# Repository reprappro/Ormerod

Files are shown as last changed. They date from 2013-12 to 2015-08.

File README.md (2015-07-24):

The RepRapPro Ormerod 2 3D Printer design files repository

Licensed under the GPL 3, see: http://www.gnu.org/copyleft/gpl.html

For more information see: https://reprappro.com/shop/reprap-kits/ormerod-2-kit/

Files in this directory were produced in SolidWorks 2015, and is the full assembly for the Ormerod 2. Some components that are shared with our other printers may be found in our "Library" repository.

The 'STLs' directory contains STLs of the printed parts. Instructions for printing parts for Ormerod 2, and a reference - itemising part numbers, descriptions and required quantities - may be found in the Ormerod instructions, here: https://reprappro.com/documentation/ormerod-2/#Printing_parts_for_Ormerod_2

The 'dxf' folder contains the parts in a format for laser cutting.

License GPL

No guarantee is made that the files contained in this project will be free from design faults. The user accepts the risk that some issues may arise from printing and assembling the files contained within this project. Users are however encouraged to publish errors/improvements back to the originator.

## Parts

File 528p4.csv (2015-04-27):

ITEM NO. | PART NUMBER | DESCRIPTION | Category | QTY.
1 | 1009 | 100M PLASTIC REEL OF 1.75 FILAMENT PLA | HARDWARE | 1
2 | 1047 | PCB HEATER (TABBED VERSION) | HARDWARE | 2
3 | 1095 | TCRT1000 | Electronics | 1
4 | 110 | M2.5X5 CAP HEAD | FASTENERS | 2
5 | 111 | M3X8 CAP HEAD | FASTENERS | 5
6 | 112 | M3X25MM CAP SCREW | FASTENERS | 7
7 | 115 | M4X8MM COUNTERSUNK SOCKET SCREW | Fasteners | 1
8 | 116 | M4X12MM COUNTERSUNK SOCKET SCREW | Fasteners | 10
9 | 125 | GLASS PRINTING PLATE | HARDWARE | 1
10 | 185 | MICROSWITCH | HARDWARE | 2
11 | 212 | M3 PLAIN WASHER | FASTENERS | 19
12 | 241 | M3X20MM CAP SCREW | FASTENERS | 2
13 | 257 | M3X12 CAP SCREW | FASTENERS | 16
14 | 258 | M3 NUT | FASTENERS | 46
15 | 279 | 623 BEARING | HARDWARE | 5
16 | 380 | M3X40 CAP HEAD | FASTENERS | 2
17 | 390 | M5X300MM THREADED ROD | Hardware | 1
18 | 394 | DUET | ELECTRONICS | 1
19 | 402 | SMOOTH ROD 12X350MM | Hardware | 4
20 | 407 | Z RUNNER MOUNT | PRINTED PARTS | 1
21 | 408 | NEMA 17 | HARDWARE | 3
22 | 414 | M6X16MM COUNTERSUNK SOCKET SCREW | Fasteners | 7
23 | 423 | MR93ZZ BEARING | Hardware | 1
24 | 424 | M4X16MM BUTTON HEAD CAP SCREW | Fasteners | 3
25 | 425 | Z NUT TRAP V2 | PRINTED PARTS | 1
26 | 429 | M3X8 COUNTERSUNK SCREW | FASTENERS | 2
27 | 437 | Z LOWER MOUNT | PRINTED PARTS | 1
28 | 438 | Z UPPER MOUNT | PRINTED PARTS | 1
29 | 440 | Z GEAR | PRINTED PARTS | 1
30 | 441 | Z GEAR DRIVEN | PRINTED PARTS | 1
31 | 442 | SPOOL SPIGOT | PRINTED PARTS | 1
32 | 443 | LM12LUU | HARDWARE | 1
33 | 444 | LM12UU | Hardware | 5
34 | 452 | 20X40 ALUMINIUM EXTRUSION 350MM | Hardware | 2
35 | 461 | M2.5X10 CAP HEAD | Fasteners | 4
36 | 462 | X IDLER BRACKET | PRINTED PARTS | 1
37 | 465 | M3X50 CAP HEAD | FASTENERS | 6
38 | 466 | M3X12 COUNTERSUNK HEAD | FASTENERS | 7
39 | 467 | M3X20MM COUNTERSUNK SOCKET SCREW | Fasteners | 1
40 | 468 | M3X25MM COUNTERCUNK SOCKET SCREW | Fasteners | 1
41 | 469 | Z MOTOR BRACE | PRINTED PARTS | 1
42 | 473 | X MOTOR BRACKET | PRINTED PARTS | 1
43 | 492 | Z BEARING CLAMP | PRINTED PARTS | 2
44 | 497 | M4 T-NUT | Fasteners | 15
45 | 498 | HEAT SPREADER | HARDWARE | 1
46 | 503 | Z FOOT | PRINTED PARTS | 1
47 | 520 | M3X35 CAP SCREW | FASTENERS | 1
48 | 527 | Z CORNER BRACKET | PRINTED PARTS | 1
49 | 529 | Y AXIS RIB | LASER CUT | 1
50 | 530 | Y AXIS CROSS RIB | LASER CUT | 1
51 | 531 | Y AXIS END PLATE | LASER CUT | 2
52 | 543 | M3X30 CAP SCREW | FASTENERS | 4
53 | 544 | M3X16MM COUNTERSUNK SOCKET SCREW | Fasteners | 4
54 | 545 | PROXIMITY SENSOR PCB | ELECTRONICS | 1
55 | 546 | X Carriage | PRINTED PARTS | 1
56 | 547 | Y IDLER BRACKET | PRINTED PARTS | 1
57 | 548 | Y MOTOR BRACKET | PRINTED PARTS | 1
58 | 549 | Y BEARING BELT CLAMP | PRINTED PARTS | 1
59 | 550 | Y BEARING CLAMP TAGGED | PRINTED PARTS | 1
60 | 561 | X AXIS PLATE | LASER CUT | 1
61 | 562 | X RIB | LASER CUT | 1
62 | 575 | BED CABLE SHIELD | Sheet | 1
63 | 576 | DUET ENCLOSURE BASE | HARDWARE | 1
64 | 577 | DUET ENCLOSURE LID | HARDWARE | 1
65 | 578 | DUET PERIMETER | HARDWARE | 1
66 | 579 | MOTOR SHIELD | SHEET METAL | 1
67 | 581 | VBFS-M3-5-16 | FASTENERS | 4
68 | 582 | MOTOR SHIELD | HARDWARE | 2
69 | 597 | REGULATOR PCB | ELECTRONICS | 1
70 | 641 | SPACER | LASER CUT | 1
71 | 642 | SPOOL MOUNT | LASER CUT | 1
72 | 651 | M4X10mm BUTTON HEAD SCREW | HARDWARE | 6
73 | 681 | BED | LASER CUT | 1
74 | 712 | M5 FULL NUT | FASTENERS | 3
75 | 818 | M3X18MM MALE/FEMALE STANDOFF VBMP-M3-5.0-18 | FASTENERS | 3
76 | 820 | PSU COVER | PRINTED PARTS | 1
77 | 821 | PSU BRACE | PRINTED PARTS | 1
78 | 822 | OUTER PSU PLATE | HARDWARE | 1
79 | 823 | PSU SPACER | HARDWARE | 1
80 | 824 | PSU COVER SPACER | HARDWARE | 1
81 | 825 | INNER PSU PLATE | LASERCUT | 1
82 | 826 | INNER PSU SPACER | LASERCUT | 1
83 | 829 | M4X50MM BUTTON HEAD SOCKET SCREW | Fasteners | 1
84 | 831 | SP-200 12V POWER SUPPLY | HARDWARE | 1

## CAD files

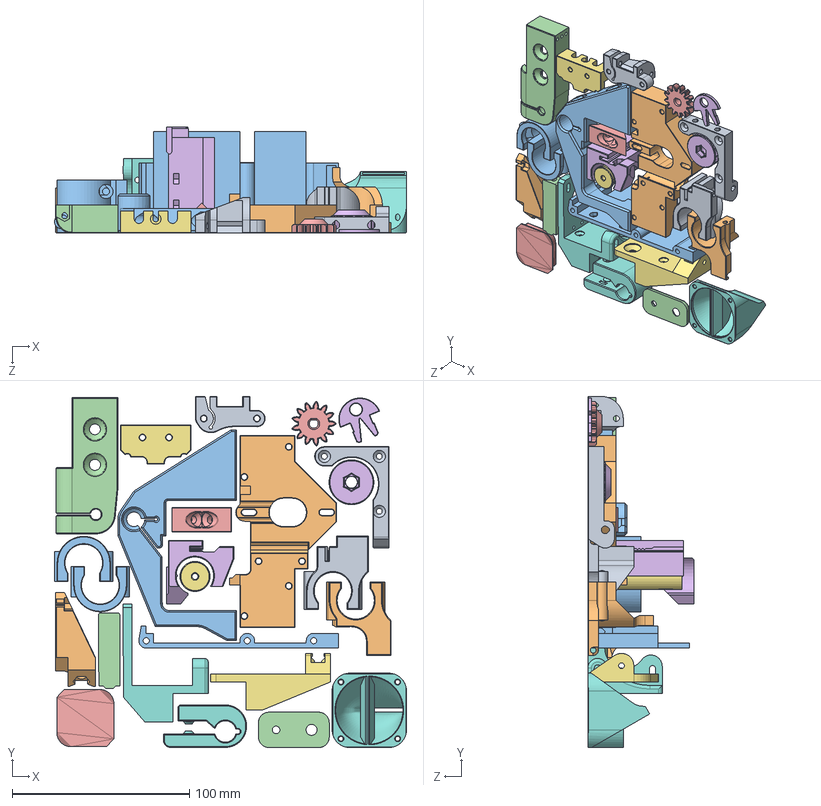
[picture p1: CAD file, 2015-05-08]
PrintTray.SLDASM
198.7 x 198.2 x 60.0 mm
logo

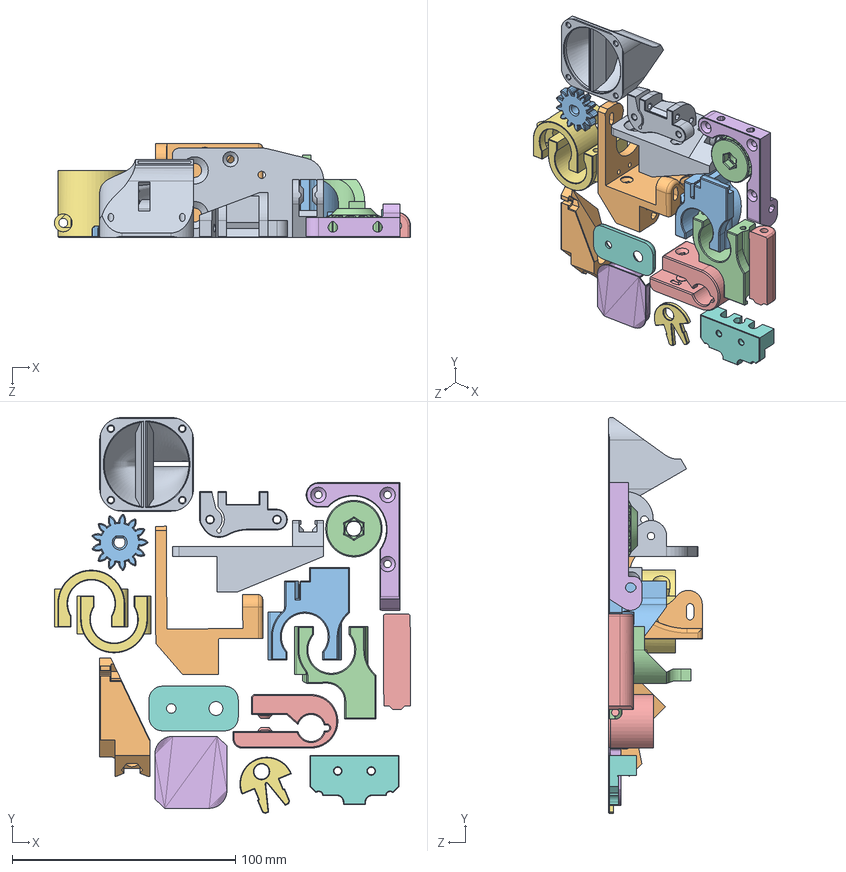
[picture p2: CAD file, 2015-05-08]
DayPrintTrays.SLDASM
159.6 x 177.4 x 42.0 mm
logo

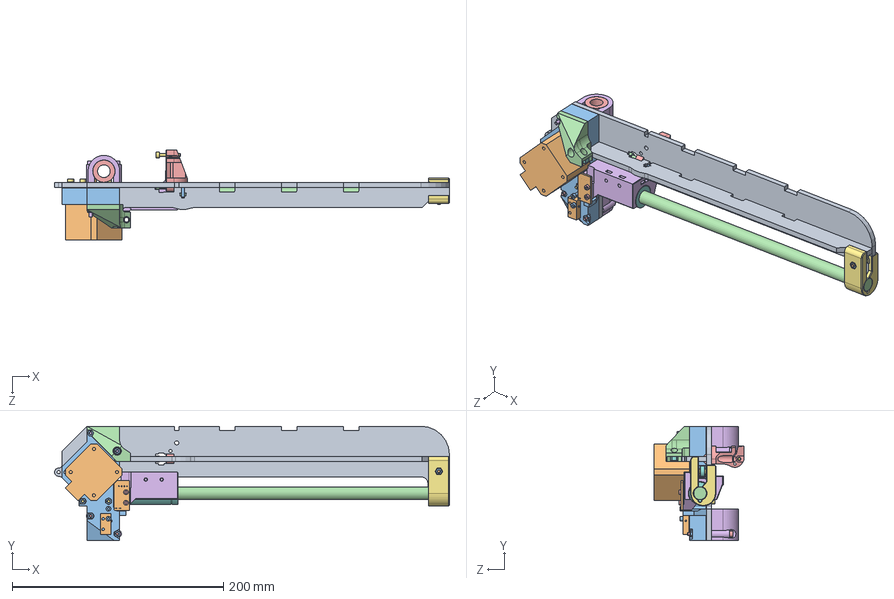
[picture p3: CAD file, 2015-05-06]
760.SLDASM
374.3 x 108.5 x 85.4 mm

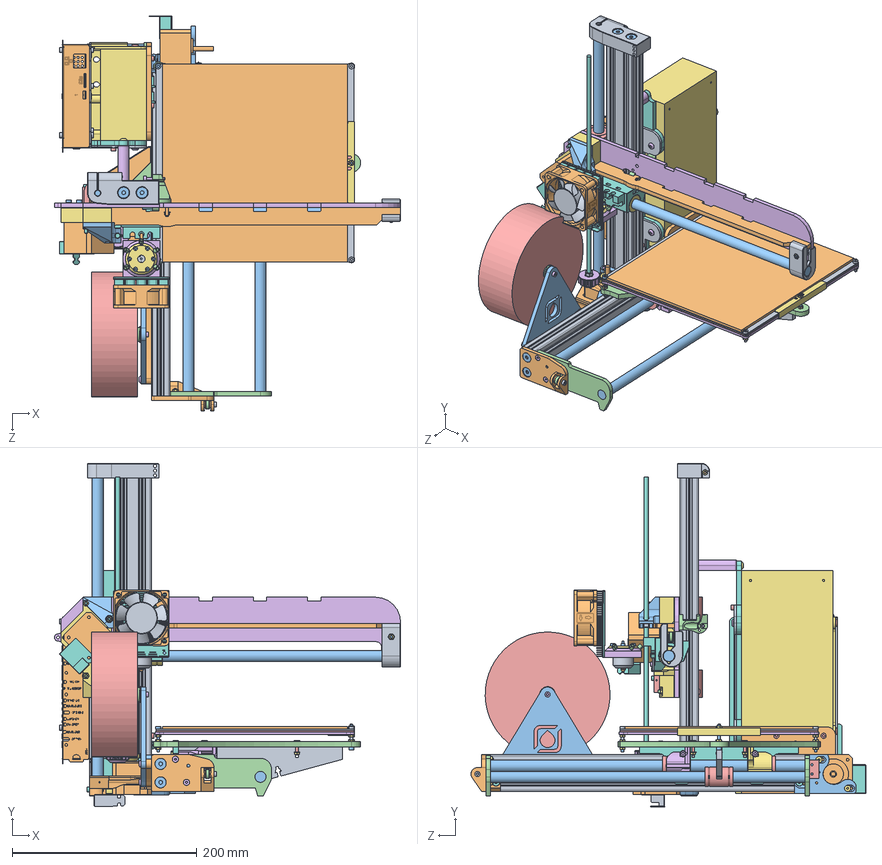
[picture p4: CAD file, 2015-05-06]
528.SLDASM
374.3 x 371.3 x 427.1 mm
Mixing Chamber
Nozzle
Mixer
ThermalBreak x 5
O-Ring
Heatsink Block Bottom
Heatsink Block Top2
m2.5cap screw x 6
60mm Heatsink

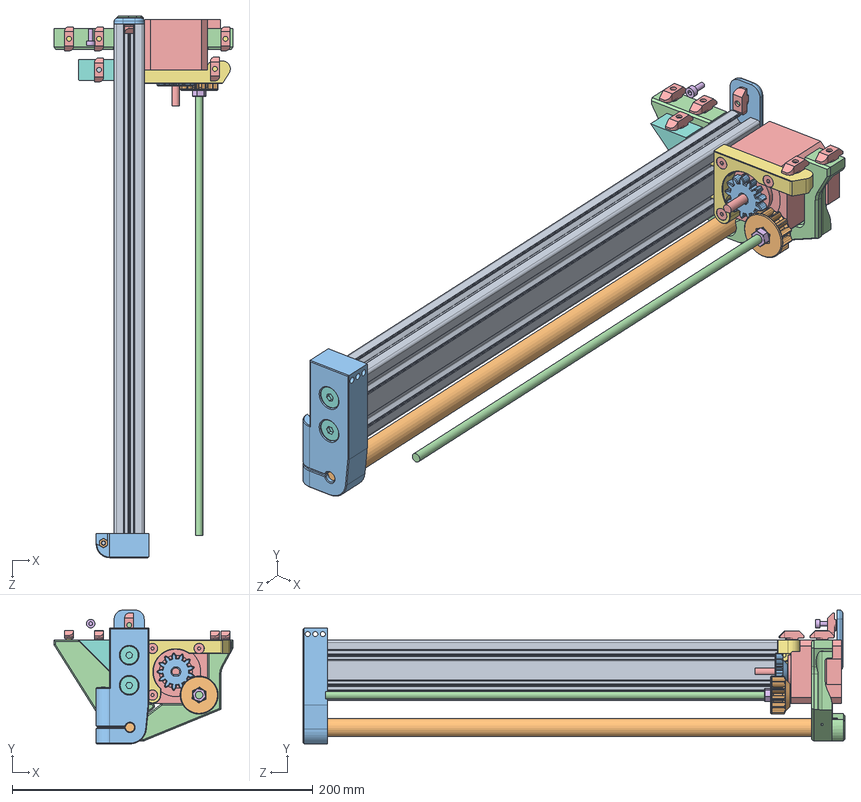
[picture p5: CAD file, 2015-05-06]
750Z.SLDASM
119.0 x 89.0 x 360.0 mm

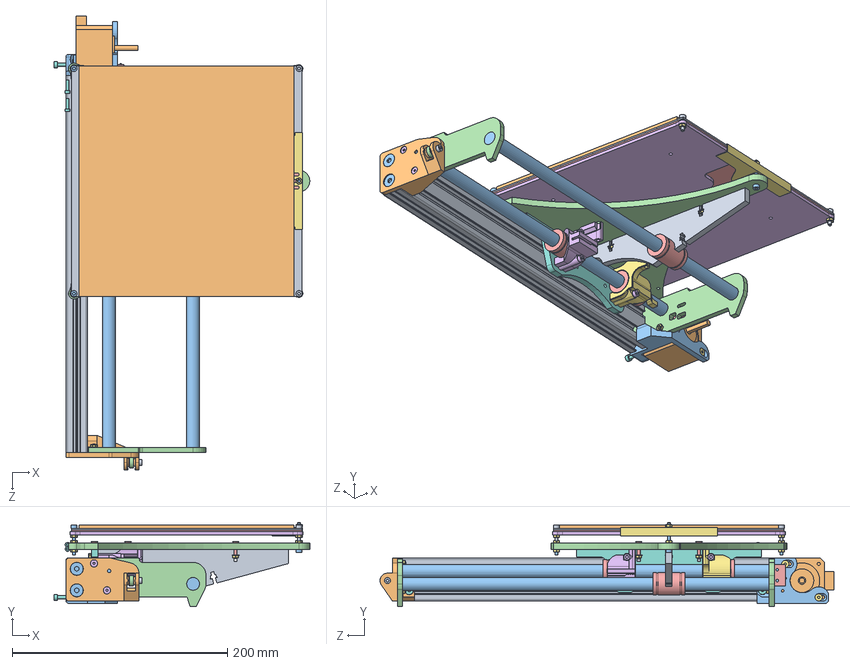
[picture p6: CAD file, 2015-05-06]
750Y.SLDASM
237.4 x 78.0 x 421.5 mm

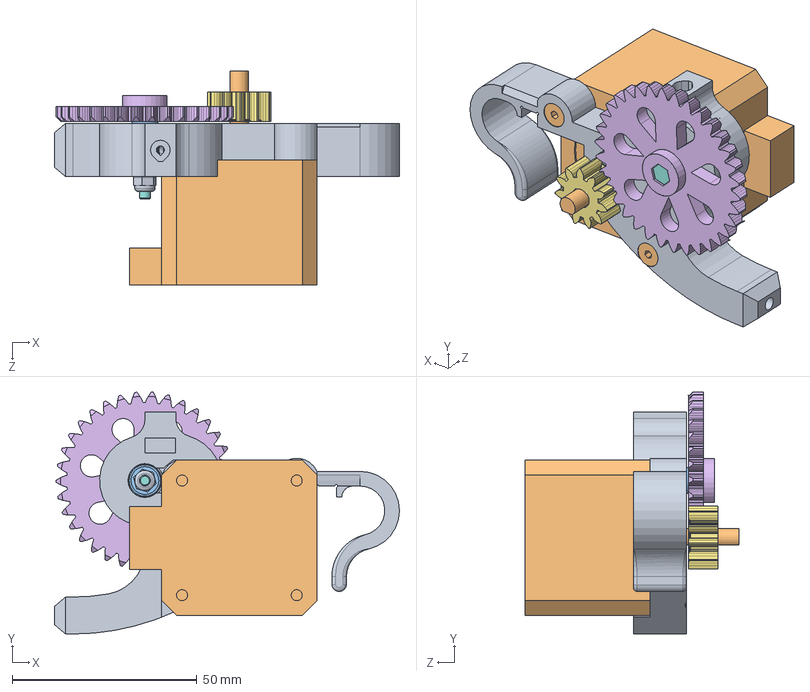
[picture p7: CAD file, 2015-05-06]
733.SLDASM
93.3 x 65.4 x 57.8 mm

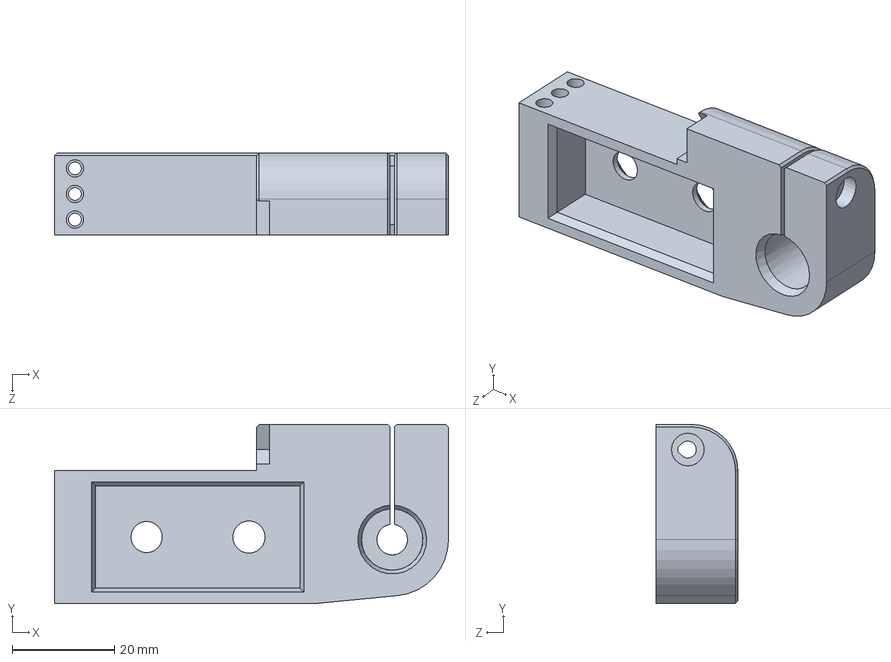
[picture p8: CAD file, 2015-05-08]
438.SLDPRT
77.0 x 35.0 x 16.0 mm

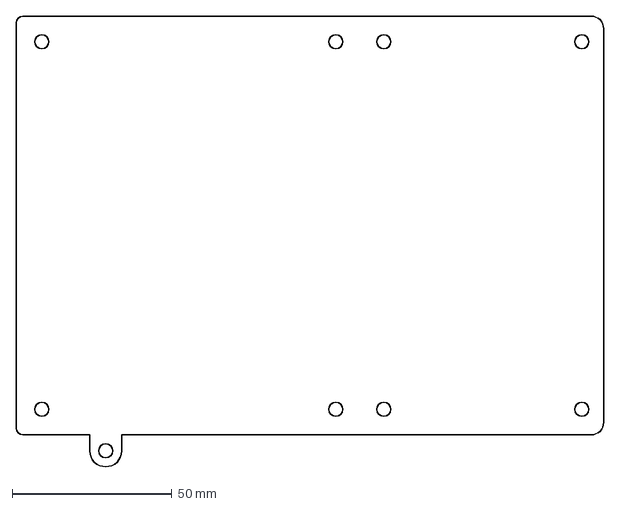
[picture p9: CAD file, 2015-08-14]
dxf/Duet-enclosure-base-expansion.DXF
183.8 x 141.0 mm

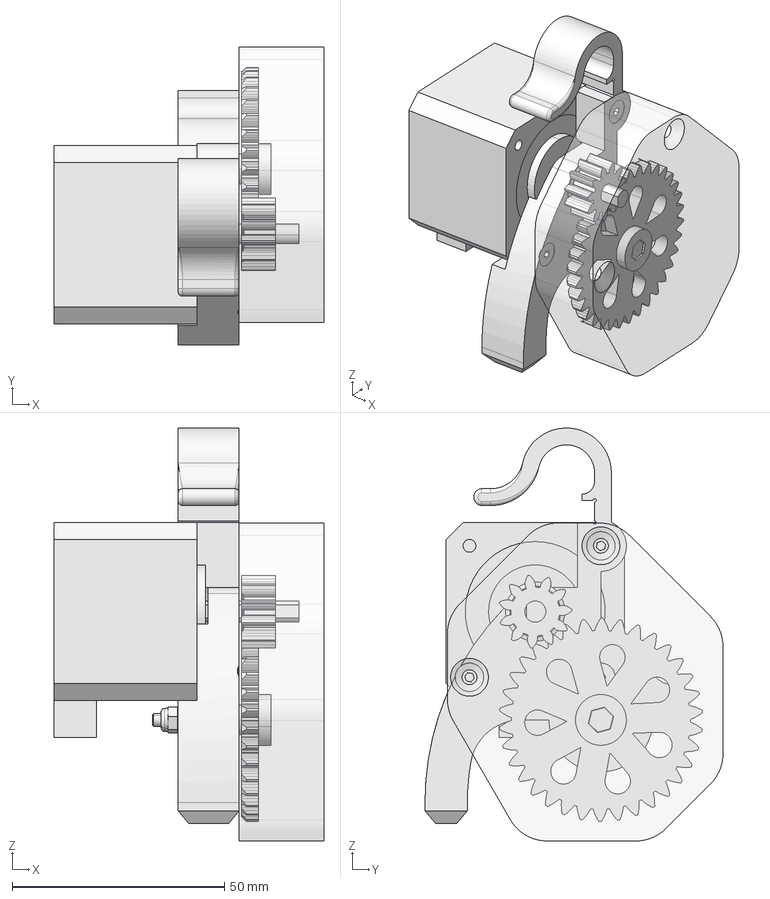
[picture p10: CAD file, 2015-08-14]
freeCAD/extruder-drive-cover.fcstd
63.6 x 70.3 x 97.4 mm
washer
nyloc-nut
big-gear
screw-1
motor
hobbed-drive
bearing-1
screw-3
small-gear
M3-hex-head-screw
screw-2
bearing-2
bearing-3
gear-cover

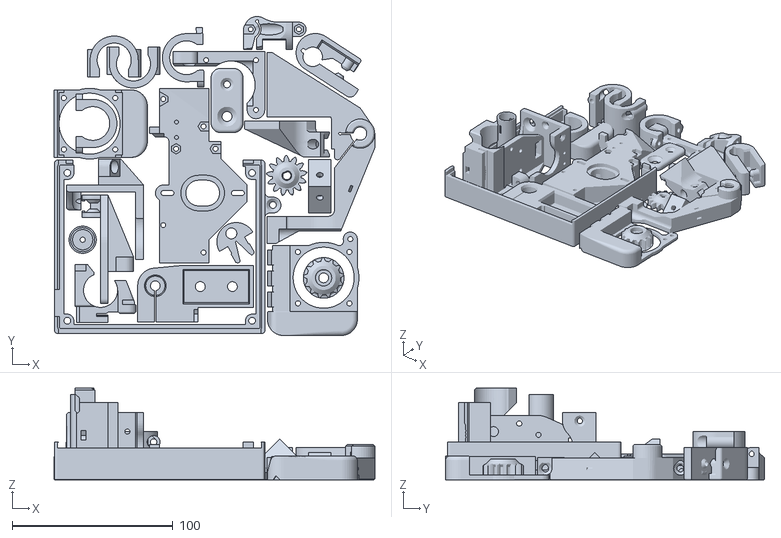
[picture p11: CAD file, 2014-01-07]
stl/build-plate.STL
199.6 x 198.6 x 57.0

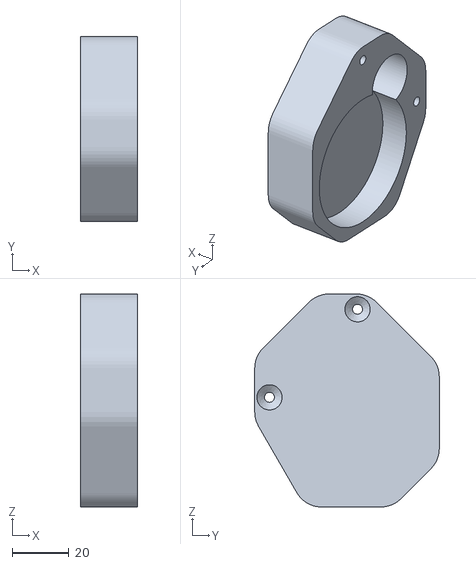
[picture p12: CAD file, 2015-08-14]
stl/individual parts/extruder-gear-cover.stl
20.0 x 65.0 x 75.0

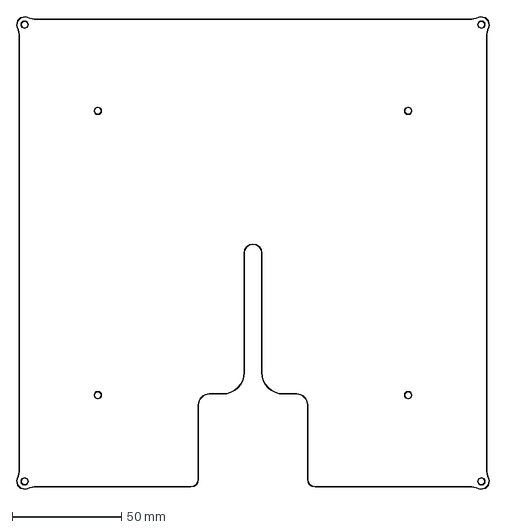
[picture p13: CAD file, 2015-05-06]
dxf/1044.1.DXF
216.6 x 216.6 mm

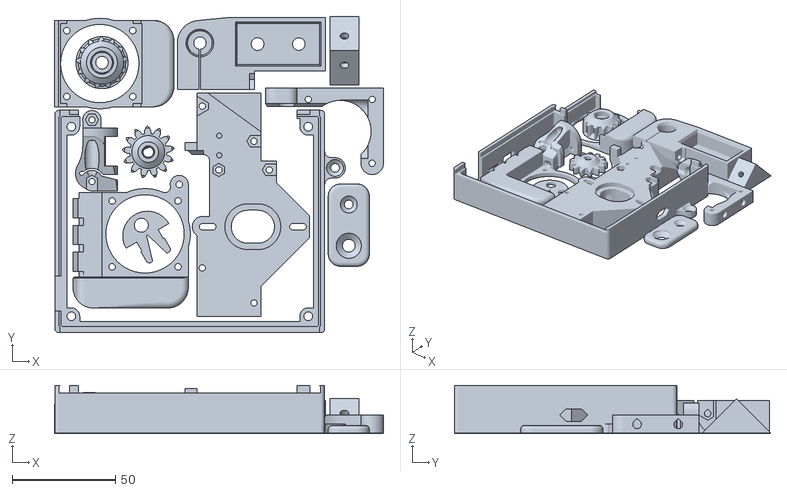
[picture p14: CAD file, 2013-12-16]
stl/build-plate_a.STL
159.7 x 153.6 x 23.5

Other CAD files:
STLs/Trays/528.5AM2.STL
STLs/Trays/528.5PMTray.STL
dxf/561.1.DXF
STLs/Trays/528.5AM1.STL
1044.SLDPRT
1079.SLDPRT
1123.SLDPRT
402.SLDDRW
402.SLDPRT
407.SLDPRT
425.SLDPRT
437.SLDPRT
440.SLDPRT
441.SLDPRT
442.SLDPRT
446.SLDPRT
447.SLDPRT
458.SLDDRW
458.SLDPRT
462.SLDPRT
469.SLDPRT
473.SLDPRT
492.SLDPRT
501.SLDPRT
503.SLDPRT
525.SLDPRT
527.SLDPRT
529.SLDPRT
530.SLDPRT
531.SLDPRT
546.SLDPRT
547.SLDPRT
548.SLDPRT
549.SLDPRT
550.SLDPRT
554.SLDPRT
561.SLDPRT
562.SLDPRT
575.SLDPRT
641.SLDPRT
642.SLDPRT
681.SLDPRT
781.SLDPRT
821.SLDPRT
STLs/1079.STL
STLs/1123.STL
STLs/407.STL
STLs/425.STL
STLs/437.STL
STLs/438.STL
STLs/440.STL
STLs/441.STL
STLs/442.STL
STLs/446.STL
STLs/447.STL
STLs/462.STL
STLs/469.STL
STLs/473.STL
STLs/492.STL
STLs/503.STL
STLs/525.STL
STLs/527.STL
STLs/546.STL
STLs/547.STL
STLs/548.STL
STLs/549.STL
STLs/550.STL
STLs/554.STL
STLs/821.STL
dxf/1044.DXF
dxf/531.1.DXF
dxf/575.0.DXF
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

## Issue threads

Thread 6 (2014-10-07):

build-plate_a.stl casues error in Slic3r 1.1.7

OricTosh, 2014-10-07:
The build plate_a  STL file for the Ormerod causes an error in Slic3r 1.1.7 it won't slice the file.
I put the file into netfabb basic and repaired the file. I'm now able to slice the file with no errors.

RRP-support, 2015-10-05:
This is an automated reply to your message "Re: [Ormerod] build-plate_a.stl casues error in Slic3r 1.1.7 (#6)" sent to support@reprappro.com.

Dear Chris Hills <notifications@github.com>

Thank you for your email. We endeavour to answer all emails within 24 hours. It may take longer during busy times, and holiday periods. We process all customer queries on a first come first served basis, during our office hours which are 9am to 5pm GMT Mon-Fri.

Other support channels are available. Please refer to the relevant troubleshooting guide for your machine:

Ormerod 2: https://reprappro.com/documentation/ormerod-2/troubleshooting/
Ormerod: https://reprappro.com/documentation/ormerod/troubleshooting/

Huxley Duo: https://reprappro.com/documentation/huxley-duo/troubleshooting/
Huxley: https://reprappro.com/documentation/huxley/troubleshooting/

Mono and Tricolour Mendel: https://reprappro.com/documentation/mendel-tricolour/troubleshooting/

Support is also available from other owners of RepRapPro and other 3D printers, either through the RepRap Forums: https://forums.reprap.org or through IRC which can be accessed from here: https://reprappro.com/support-channel/ (works on Chrome, not Firefox).

Best regards,

RepRapPro Support Team.

RRP-support, 2015-10-05:
Is that one of the build plates for the Ormerod 1 384 or Ormerod 2 528.4? It's probably better use the latest parts, unless you need the Ormerod 1 y-axis parts, in which case just print them.
Ian
RepRapPro tech support.

OricTosh, 2015-10-05:
Hi Ian,

Yes it was a build plate for an ormerod 2 528.4;
I closed the issue as it was sometime ago and has probably been fixed
with a newer set of STL files as you suggested, so no need to keep it open.

Regards
Chris Hills

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

RRP-support, 2015-10-05:
Ah! Yes, now I see. Thanks!
Ian
RepRapPro tech support

Closed 2015-10-05.

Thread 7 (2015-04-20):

Impossible to know what anything is.....

shadow651, 2015-04-20:
The way this library is now set up (all files are numbered, I assume using some internal part number system), there is no way to know what any file is without opening them. This makes searching for anything specific particularly difficult.

It would be great if a key listing each part and it's corresponding number could be added.

RRP-support, 2015-04-20:
This is an automated reply to your message "[Ormerod] Impossible to know what anything is..... (#7)" sent to support@reprappro.com.

Dear Joseph Dufour <notifications@github.com>

Thank you for your email. We endeavour to answer all emails within 24 hours. It may take longer during busy times, and holiday periods. We process all customer queries on a first come first served basis, during our office hours which are 9am to 5pm GMT Mon-Fri.

Other support channels are available. Please refer to the relevant troubleshooting guide for your machine:

Ormerod 2: https://reprappro.com/documentation/ormerod-2/troubleshooting/
Ormerod: https://reprappro.com/documentation/ormerod/troubleshooting/

Huxley Duo: https://reprappro.com/documentation/huxley-duo/troubleshooting/
Huxley: https://reprappro.com/documentation/huxley/troubleshooting/

Mono and Tricolour Mendel: https://reprappro.com/documentation/mendel-tricolour/troubleshooting/

Support is also available from other owners of RepRapPro and other 3D printers, either through the RepRap Forums: https://forums.reprap.org or through IRC which can be accessed from here: https://reprappro.com/support-channel/ (works on Chrome, not Firefox).

Best regards,

RepRapPro Support Team.

reprappro, 2015-04-20:
And there is. The README mentions the BOM.xlsx file which lists all the part numbers and descriptions.

RRP-support, 2015-04-20:
This is an automated reply to your message "Re: [Ormerod] Impossible to know what anything is..... (#7)" sent to support@reprappro.com.

Dear reprappro <notifications@github.com>

Thank you for your email. We endeavour to answer all emails within 24 hours. It may take longer during busy times, and holiday periods. We process all customer queries on a first come first served basis, during our office hours which are 9am to 5pm GMT Mon-Fri.

Other support channels are available. Please refer to the relevant troubleshooting guide for your machine:

Ormerod 2: https://reprappro.com/documentation/ormerod-2/troubleshooting/
Ormerod: https://reprappro.com/documentation/ormerod/troubleshooting/

Huxley Duo: https://reprappro.com/documentation/huxley-duo/troubleshooting/
Huxley: https://reprappro.com/documentation/huxley/troubleshooting/

Mono and Tricolour Mendel: https://reprappro.com/documentation/mendel-tricolour/troubleshooting/

Support is also available from other owners of RepRapPro and other 3D printers, either through the RepRap Forums: https://forums.reprap.org or through IRC which can be accessed from here: https://reprappro.com/support-channel/ (works on Chrome, not Firefox).

Best regards,

RepRapPro Support Team.

shadow651, 2015-04-20:
This list appears to be incomplete, I can't find the nozzle mount on it (maybe this is a separate issue)

I assume that the Nozzle mount is shared by multiple printers, and thus would be in the Library repository, but that one doesn't appear to have a key.

RRP-support, 2015-04-20:
This is an automated reply to your message "Re: [Ormerod] Impossible to know what anything is..... (#7)" sent to support@reprappro.com.

Dear Joseph Dufour <notifications@github.com>

Thank you for your email. We endeavour to answer all emails within 24 hours. It may take longer during busy times, and holiday periods. We process all customer queries on a first come first served basis, during our office hours which are 9am to 5pm GMT Mon-Fri.

Other support channels are available. Please refer to the relevant troubleshooting guide for your machine:

Ormerod 2: https://reprappro.com/documentation/ormerod-2/troubleshooting/
Ormerod: https://reprappro.com/documentation/ormerod/troubleshooting/

Huxley Duo: https://reprappro.com/documentation/huxley-duo/troubleshooting/
Huxley: https://reprappro.com/documentation/huxley/troubleshooting/

Mono and Tricolour Mendel: https://reprappro.com/documentation/mendel-tricolour/troubleshooting/

Support is also available from other owners of RepRapPro and other 3D printers, either through the RepRap Forums: https://forums.reprap.org or through IRC which can be accessed from here: https://reprappro.com/support-channel/ (works on Chrome, not Firefox).

Best regards,

RepRapPro Support Team.

RRP-support, 2015-04-20:
For currently shipping Ormerod kits (up to 528.4) it's probably easiest to look at the 'release' section of the github repository, here: https://github.com/reprappro/Ormerod/releases
Either download the one appropriate to your machine, or click on the 'tag' link to take to the repository, as it looked at that time; eg 528.4 is here: https://github.com/reprappro/Ormerod/tree/528.4
This gives you all the files, as they came with your machine, and parts are named with a description. If you need other specific parts that we have omitted, let me know.
We are in the midst of restructuring our github files. We will be using part numbers for the part names from now on, but they will be referenced in the instructions, and tie in with the bags that the parts were supplied in, as well as listed in the BoM. This work is on-going, and not fully completed yet.

Ian
RepRapPro tech support

shadow651, 2015-04-20:
Ok, Closing issue.

Thanks for the quick response.

Closed 2015-04-20.

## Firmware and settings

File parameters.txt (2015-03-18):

"y-cross-rib-thickness"=6
"y-rib-thickness"=6
"bed-plate-thickness"=6
"x-plate-thickness"=5
"rod-diameter"=12
"t-nut-hole-diameter"=3
"y-plate-thickness"=5
"enclosure-thickness"=0.6
"M3-Clearance"=3.3
"M4-Clearance"=4.3
"M5-Clearance"=5.3
"M6-Clearance"=6.3
"M8-Clearance"=8.3
"623-Bearing-Dia"=11.2
"MR93ZZ-Bearing-Dia"=9.1

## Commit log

2013-12-02 Ormerod launch.
    [#x-axis-plate.DXF, 40x20-fan.SLDPRT, 40x20_extrusion.SLDDRW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]
2013-12-02 Individual STL files added.
    [y-bearing-clamp.STL, Duet-enclosure.STL, fan-duct.STL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]
2013-12-02 Extruder drive STL files added.
    [extruder-drive-block.STL, large-gear.STL, small-gear.STL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]
2013-12-03 nozzle-mount STL file added.
    [nozzle-mount.STL]
2013-12-07 Retaining tongue added to STLs.
    [tongue.stl]
2013-12-11 z-nut-trap tweaked to strengthen x-rib
    [build-plate_a.SLDASM, build-plate_a.STL, build-plate_b.STL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]
2013-12-11 STL files re-generated.
    [y-bearing-clamp.STL, Duet-enclosure.SLDPRT, Duet-enclosure.STL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]
2013-12-16 adjustable z-runner-mount.
    [Duet-enclosure.STL, Duet-enclosure.stl, Ormerod.SLDASM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]
2013-12-19 Y axis end plates renamed. New logo added.
    [Duet-enclosure-base.DXF, Duet-enclosure-base.SLDPRT, Ormerod.SLDASM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]
2014-01-07 insulator dxf modified to be symmetrical.
    [Ormerod.SLDASM, build-plate.SLDASM, build-plate.STL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]
2014-02-07 Four point mounting Y axis.
    [Duet-enclosure.SLDPRT, Duet-enclosure.stl, M3x30-cap-head.SLDPRT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]
2014-02-11 6mm 3-point Y axis.
    [bed.DXF, bed.SLDPRT, parameters.txt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]
2014-03-26 before tin enclosure.
    [Duet-enclosure-base.DXF, Duet-enclosure-base.SLDPRT, Duet-enclosure-lid.SLDPRT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]
2014-04-07 Y and Z bar clearances added.
    [Ormerod.SLDASM, bed.DXF, build-plate.SLDASM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]
2014-04-21 Etched enclosures.
    [#Flat-Pattern(8) - Duet-enclosure-lid.DXF, Duet-enclosure-base.DXF, Duet-enclosure-base.SLDPRT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]
2014-05-09 X carriage modified with elongated idler bearing slot, clearance for four wire proximity sensor board, and location dimples to fit into the linear bearing grooves.
    [x-carriage.SLDPRT, x-carriage.stl]
2014-06-11 Spool mount added. PSU mounting improved.
    [Duet-enclosure-base.DXF, Duet-enclosure-base.SLDDRW, Duet-enclosure-base.SLDPRT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]
2014-06-30 profiles tweaked.
    [Duet-enclosure-base.DXF, Duet-enclosure-base.SLDDRW, Duet-enclosure-base.SLDPRT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]
2014-07-09 ac-cover modified for better fit.
    [Ormerod.SLDASM, ac-cover.SLDPRT, ac-cover.STL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]
2014-07-25 ac-cover modified to allow for ground connection.
    [ac-cover.SLDPRT, ac-cover.STL]
2014-08-21 ac-cover clearance added for Y axis tensioning M3 screw.
    [Ormerod.SLDASM, ac-cover.SLDPRT, ac-cover.STL]
2014-08-26 Power supply fan mount added.
    [PSFANMount.scad, PSFANMount.stl]
2014-08-31 Final commit before Ormerod 2 release.
    [Duet-enclosure.stl, M3x12-cap-head.SLDPRT, extruder-drive-block.stl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]
2014-08-31 Enclosures modified for better fit.
    [40x20-fan.SLDPRT, 40x20_extrusion.SLDPRT, 576.1 Duet-enclosure-base.DXF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]
2014-09-01 stl files updated for Ormerod 2.
    [M3x12-cap-head.SLDPRT, Ormerod.SLDASM, build-plate.SLDASM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]
2014-09-12 Updating hole sizes for production
    [ac-cover.SLDPRT, extruder-drive-block.SLDPRT, extruder-drive-plate.SLDASM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]
2014-09-12 Assembly model mating errors eliminated. Enclosure drawings added.
    [575.0 bed-cable-shield.DXF, 578.0 enclosure-perimeter.DXF, M3x12-cap-head.SLDPRT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]
2014-10-20 Hole sizes tweaked.
    [Ormerod.SLDASM, ac-cover.SLDPRT, ac-cover.STL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]
2014-10-24 Chamfers modified to make the parts easier to print.
    [extruder-drive-block.SLDPRT, extruder-drive-block.stl, z-lower-mount.SLDPRT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]
2014-10-28 fan ducts replaced with lasercut spacer for future mounting of controllable cooling fan.
    [Ormerod.SLDASM, ac-cover.SLDPRT, enclosure.SLDASM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]
2014-10-30 Started work on the cear covers.
    [end-plate.stl, extruder-drive-cover.fcstd, magnet-mount.stl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]
2014-12-23 PSU changed to SP-200-12.
    [40x10-fan.SLDPRT, 578.1 enclosure-perimeter.DXF, 820-psu-cover.SLDPRT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]
2015-03-03 Quick set nozzle mount
    [1079.SLDPRT, 1079.STL]
2015-03-04 New PSU mounting. Quick-set dual nozzle modifications.
    [1044-bed-insulator.DXF, 1044-bed-insulator.SLDPRT, 40x10-fan.SLDPRT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]
2015-03-18 Updating to use Library
    [#Flat-Pattern(8) - Duet-enclosure-lid.DXF, #x-axis-plate.DXF, 1044-bed-insulator.DXF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]
2015-04-27 Uploading some missing files
    [1044.1.DXF, 1044.SLDPRT, 1079.SLDPRT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]
2015-05-06 Updated for 528.5
    Extra holes in PCB insulator for bed clips
    Ormerod now uses quickset nozzle as standard
    Fan duct included in kit
    [1044.1.DXF, 1044.SLDPRT, 1123.STL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]
2015-05-06 Reorienting STLs
    [1123.STL, 546.STL]
2015-05-08 Tweaking Fan Duct for quickset
    [1123.SLDPRT, 1123.STL, 438.SLDPRT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]
2015-08-14 Extruder drive cover added, in case it's ever needed.
    [Duet-enclosure-base-expansion.DXF, extruder-drive-cover.fcstd, extruder-gear-cover.stl]
